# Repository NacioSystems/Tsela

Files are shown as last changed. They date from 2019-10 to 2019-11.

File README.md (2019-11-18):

# Tsela
## de NacioSystems:

Versión 1.3
Fecha: 31/10/2019

Este proyecto es un vehículo autónomo llamado **Tsela** (Tesela), que es capaz de conducir sin piloto por una pista de *siguelineas*. Realizado por NacioSystems (O Milladoiro):

Es un proyecto que tenía pensado desde hace un par de años, al ver las competiciones de siguelienas en la **Oshwdem Coruña**, y ver que todos los vehículos giran sobre dos o cuatro ruedas, pero forzando la velocidad de un lado respecto del otro, cuando en la práctica, salvo los vehículos con cadenas, todos los vehículos se mueven girando uno de los ejes, normalmente el delantero, haciendo coincidir la direccion de las ruedas delanteras con la secante de la curva.

Realmente al ver el resultado final, y las aprariencias del modelo, se me ocurrió llamarle Nisan Patrol, pero ese nombre ya estaba pillado. Me acordé también de Nicola Tesla, un pionero de los generadores eléctricos, pero el nombre tambien estaba pillado. Entonces recordé que las teselas, esos elementos geométricos que forman parte de la naturaleza, que fueron uno de los retos de la Oshwdem hace un par de años, podrían ser la clave. Así que me pareció muy apropiado el nombre de Tesela. Para abreviar, _**Tsela, Modelo 3, con Autopilot**_. :-)

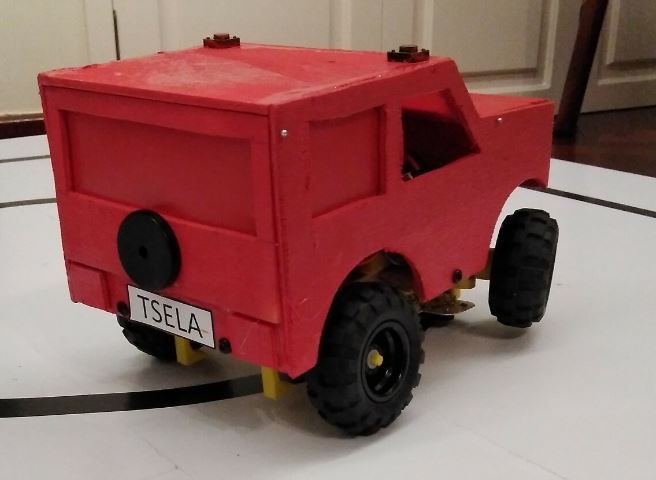
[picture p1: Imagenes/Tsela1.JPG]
Tesla Tsela M3 con Autopilot


- - -

### Introducción:

El chasis del vehículo está construido totalmente en madera, utilizando sobrante de madera de una caja de vino. Como motores utiliza dos micrometal que encontré perdidos y de los que desconozco su relación de reducción, aunque puedo decir que son muy potentes y poco veloces. Para controlar la velocidad de los motores utilizo un *driver* puente en H tipo **L298N**, que me permite regular la velocidad y el sentido de los dos motores. Por otra parte para leer la posición del vehículo respecto de la línea (negra) que debe seguir, utilizo una batería de cuatro sensores **CNY70**, puestos de modo transversal a la línea. Todo el conjunto está controlado por un **Arduino Nano** montado sobre una placa de expansión. La gracia del vehículo respecto de otros siguelíneas tradicionales, a parte de su bonito diseño totalmente artesano, es que gira gracias a un eje directriz delantero movido por un microservo **SG90**. Se alimenta todo el conjunto a través de dos baterías **LiPo 18650** puestas en serie, con 8V de tensión nominal.

El vehículo se enciende por un interruptor que da tensión al *driver* de los motores y a la placa Arduino. La marcha se inicia pulsando un botón que pone el vehículo en estado *Autopilot*, que se encuentra en el techo, iniciando el movimiento hacia adelante y leyendo lo sensores infrarrojos. En función de la señal que reciba de los sensores, en caso de no estar centrado sobre la línea, manda una señal al microservo de la dirección para corregir la posición y centrarse en la línea.

A través del puerto serie permite la **conexión remota por _Bluetooth_** y la gestión del vehículo, desactivando el *Autopilot* previamente. En caso de estar activado el _Autopilot_ no seguirá las instrucciones del piloto, salvo que no encuentre una línea a seguir, en ese caso, si encuentra una línea a seguir, tendrá prefrencia el seguimiento de la línea.

Si se toma el control por Bluetooth (9600,N,1), el Autopilot se puede activar o desactivar enviando el caracter 'P'. Es recomendable poner la aplicacion Bluetooth en modo repetitivo, con lo que se consigue girar progresivamente o acelerar mientras se pulsa botón correspondiente de la app. (ejemplo Bluetooth spp pro). Otras funciones implementadas para el contros serie son:
* 'A' Avanza más rápido, acelera
* 'R' Reduce la velocidad, decelera
* 'D' Mueve la dirección hacia la derecha, muy poco respecto de la posicióin actual
* 'I' Mueve la dirección hacia la izquierda, muy poco respecto de la posición actual
* 'P' Cada pulsación cambia entre modo _Autopilot_ o modo manual
* '0' Para los motores y pone la dirección recta
* 'C' Toca el claxon

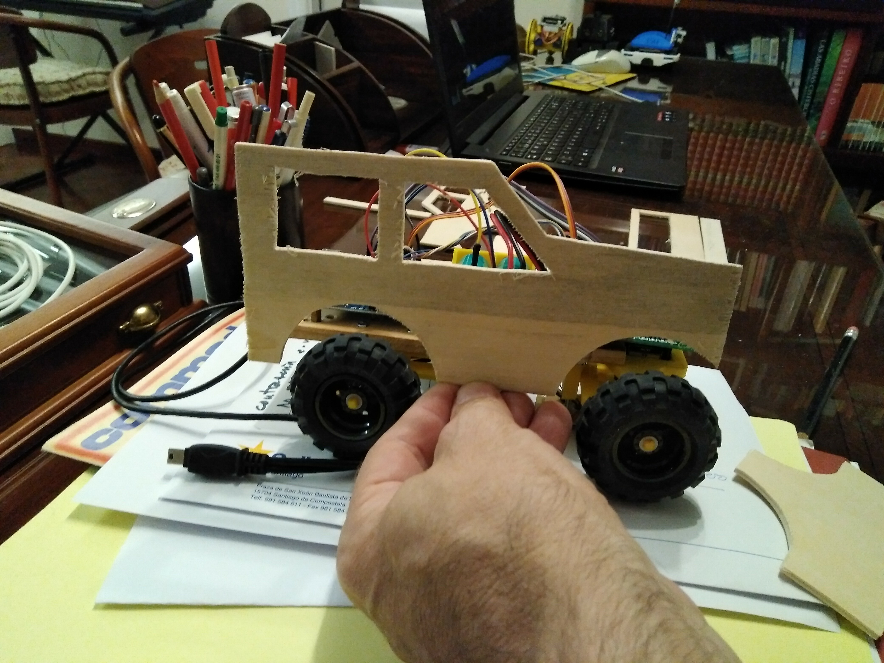
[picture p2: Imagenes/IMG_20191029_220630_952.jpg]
Imagen Tesla Tsela en construcción


Los sensores infrarrojos están montados sobre una placa improvisada, utilizando una tarjeta comercial tipo, numerados de izquierda a derecha del 1 al 4. Cuando el vehículo está centrado los sensores centrales 2 y 3 estarían sobre la línea negra, devolviendo muy poca señal al sensor, mientras que el resto de los sensores, 1 y 4 estarían sobre el blanco de la pista, devolviendo mucha señal al sensor. El sensor sobre la pista puede estar en 8 posiciones distintas:
* 1)- Sensor 1 en negro y resto en blanco. Vehículo muy desviado a la izquierda
* 2)- Sensor 1 y 2 en negro y resto en blanco. Vehículo desviado a la izquierda
* 3)- Sensor 2 en negro y resto en blanco. Vehículo ligeramente desplazado hacia la izquierda
* 4)- Sensores 2 y 3 en negro y 1 y 4 en blanco. Vehículo centrado, posición ideal
* 5)- Sensor 3 en negro y resto en blanco. Vehículo ligeramente desviado a la derecha
* 6)- Sensor 3 y 4 en negro y resto en blanco. Vehículo desviado a la derecha
* 7)- Sensor 4 en negro y resto en blanco. Vehículo muy desviado a la derecha.
* 8)- Todos los sensores sobre blanco, fuera de pista

Placa receptores infrarrojos Batería de sensores infrarrojos

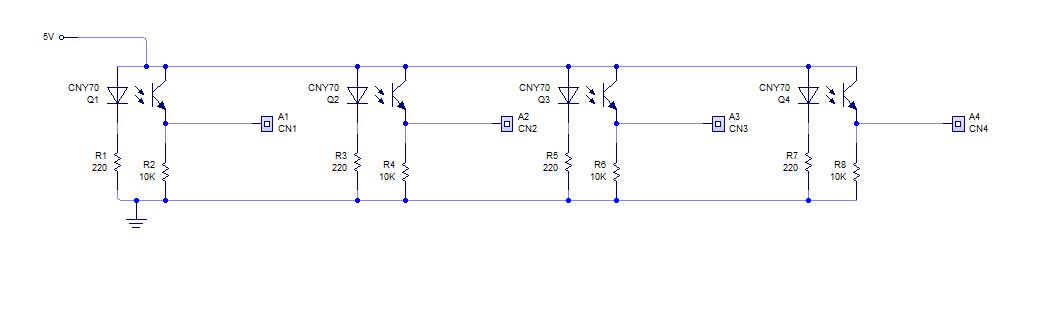
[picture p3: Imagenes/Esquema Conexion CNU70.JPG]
Esquema conexionado sensores infrarrojos Esquema de conexionado


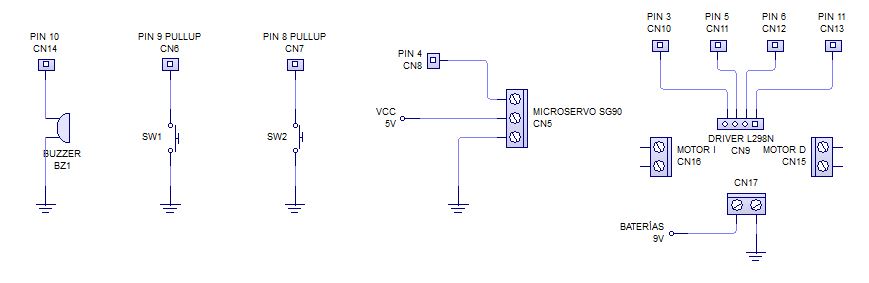
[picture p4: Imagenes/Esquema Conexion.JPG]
Esquema conexión pines Esquema conexionado pines


Conociendo la ubicación del vehículo sobre la pista, el sistema de control puede actuar sobre los motores y la dirección para corregir la posición, si es necesario, siendo los giros más cerrados cuanto más desviado está de la posición ideal, que sería cuando el vehículo está centrado.

Si el vehículo está centrado avanza recto a la máxima velocidad, pero cuando llega a una curva, detecta que es un giro por la posición de los sensores y decide reducir la velocidad y girar el eje delantero para corregir la posición.

Si la curva es muy cerrada y va muy rápido, detectará el cambio de dirección pero es posible que pierda la señal de la línea negra, lo que sería una situación fuera de pista, entonces mantendrá una velocidad más reducida y la dirección girada totalmente hasta que recupere la línea y pueda seguir el camino.

### Materiales y materiales reciclados:
El vehículo utiliza los siguientes materiales reciclados, que se pueden visualizar en las imágenes:
* Chasis y bastidor totalmente de madera, de una vieja caja de vino
* La placa que soporta los sensores es una tarjeta comercial tipo tarjeta de crédito.
* Los ejes de la dirección son metálicos de un viejo camión de bomberos de juguete
* Las ruedas son de un _quad_ Lego en desuso
* El altavoz _Buzzer_, también recuperado de un viejo juguete, que va en el portón trasero
* Parte del cableado está basado en líneas de pares telefónicos reutilizados y cable bililar de audio
* Las baterías LiPo 18650 son recuperadas de un viejo portátil que iba al desguace
* Parte de la tornillería es de una vieja impresora HP Laserjet que tambien se envió al desguace
* Los bornes y muelles del portabaterías son reutilizados de un control remoto de TV que no funcionaba
* Para las bisagras del portón trasero y del capó delantero utilizo alfileres del empaquetado de los que traen la camisas de vestir
* Los cristales tintados son trozos recortados de una separata de plástico, de las que se utilizan en carpetas de anillas perforadas.

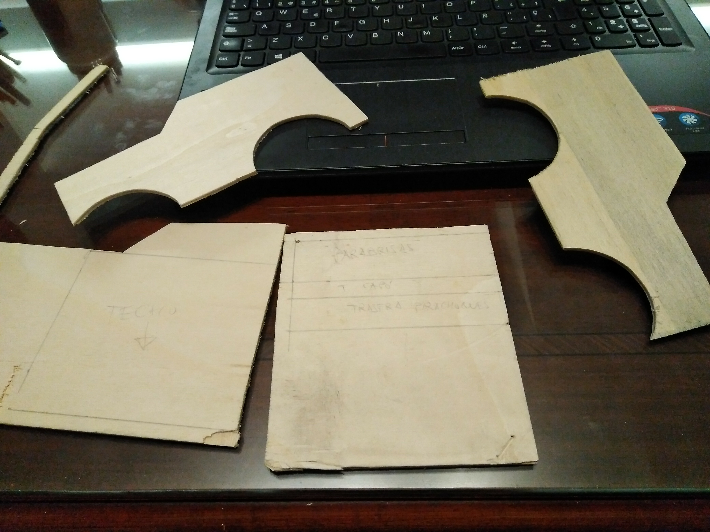
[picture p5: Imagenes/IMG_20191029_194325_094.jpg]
Foto Maderas cortadas Preparando la carrocería


Otros materiales:

También se han utilizado piezas impresas en 3D, para hacer la dirección, puesto que no servía ninguna dirección adecuada para este vehículo. La dirección es diseñada totalmente por mi, para integrar el Servo SG90, los ejes de dirección metálicos disponibles y las ruedas de Lego. Otras piezas impresas son la caja soporte de las baterías, también diseñada por mi y las piezas soporte de los motores al chasis. Para las piezas impresas he utilizado nueva tornillería de métrica M3.

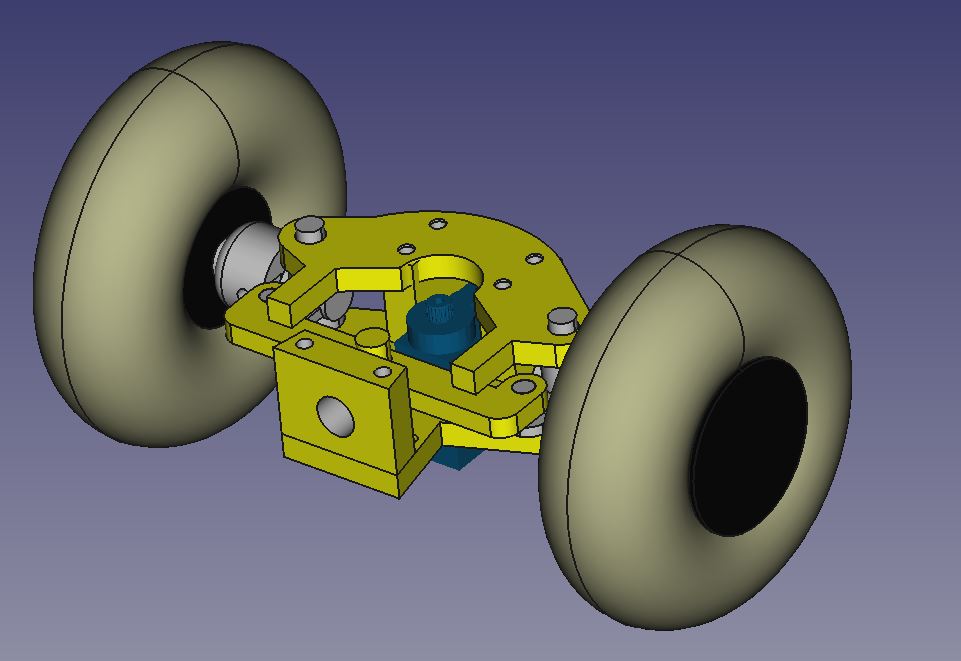
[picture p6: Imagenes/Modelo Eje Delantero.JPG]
Diseño sistema dirección Eje delantero


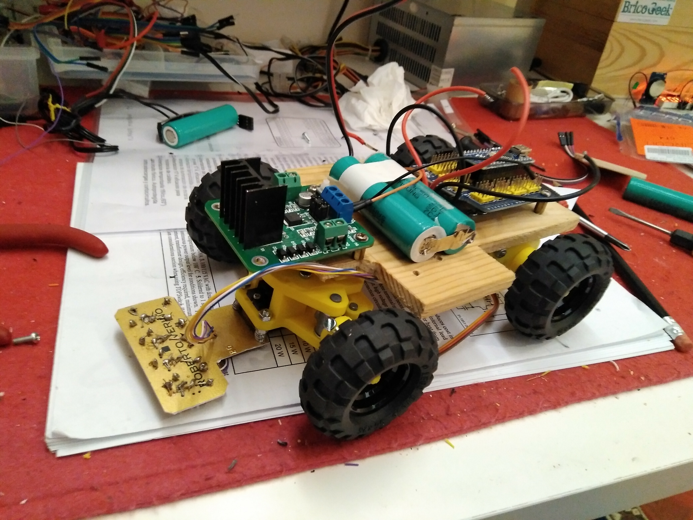
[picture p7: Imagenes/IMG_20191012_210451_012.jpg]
Foto Tsela sin carcasa Prototipo 2


Materiales electrónicos:

* [Arduino Nano][2]
* [Extension Board Arduino Nano][3]
* [Puente H L298N][4]
* [2 x Micrometal Gear. Micromotores 6V][5]
* [Microservo SG90][6]
* [4 Sensores infrarrojos CNY70][7]
* [2 LiPo 18650 de 3,7V][8]
* 2 pulsadores y un micorinterruptor
* Buzzer
* Algunas resistencias para la polarización de los CNY70 y la medición del estado de las baterías (sin implementar por A0)
* Otro pequeño material como bornas para la conexion de la batería y PCB prototipo para el montaje de interruptor y botones.

### Pista:
La pista del circuito a recorrer está montada en un tablero de 2x2m2, de color blanco, en el que se traza una línea negra de 1,9cm de ancho, que será la que marque el circuito a recorrer.

El recorrido del circuito es cerrado, los puntos de salida y llegada son el mismo. Tendrá una longitud aproximada de 4 metros e incluye rectas y curvas de diferentes radios. La curva de menor radio no será inferior a los 125 mm, y la distancia mínima entre dos partes próximas del recorrido no será inferior a los 250 mm. Las medidas y recorrido del circuito no se darán a conocer hasta el comienzo de la prueba.

Los vehículos (robots) deberán completar un recorrido completo en el menor tiempo posible.

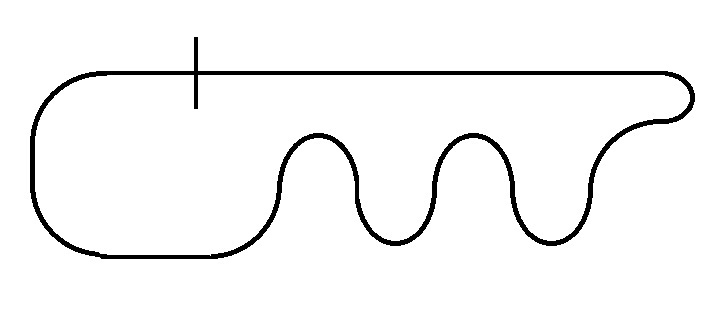
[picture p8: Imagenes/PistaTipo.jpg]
Foto Pista Modelo Pista


### Condiciones iniciales:
En el inicio de la competición el vehículo se sitúa centrado sobre la línea del circuito, en la dirección a recorrer. El interruptor de encendido debe estar en **ON** y en el momento de salida habrá que iniciar el camino pulsando el botón de *Autopilot*. Deberá realizar el recorrido en el menor tiempo posible sin salirse del circuito y recorriéndolo completamente. Una vez terminado el recorrido se puede desactivar el modo _Autopilot_ pulsando nuevamente en el botón correspondiente, o a través de Bluetooth de ser el caso.

### Desplazamientos y giros:
Una vez puesto en marcha el vehículo inicia su movimiento a la máxima velocidad, manteniendo la dirección si está centrado. En el momento que detecta que no está centrado, inicia un giro del eje delantero, a través del Microservo SG90 para corregir su posición. Una vez se encuentra centrado de nuevo, el robot devuelve la dirección del eje delantero para continuar en línea recta.

### Programa:
El programa está realizado con el IDE Arduino, para su programación directa a través de cable USB. En la carpeta software se puede ver el programa comentado. El programa cuenta con una pestaña de _"configuracion.h"_, en donde está el _pineado_ para las conexiones con el Arduino (sensores, microservo, botones, buzzer) para ajustar los valores por defecto, que dependerán de los motores y sensores utilizados en cada caso, si son diferentes a los de esta construcción. El programa está estructurado y comentado con lo que resulta fácil su comprensión, mantenimiento y modificación.

### Construcción:
El resultado final es la progresión de varias experiencias sobre el modelo inicial trabajando únicamente sobre un bastidor de madera, al que fui añadiendo modificaciones según iban apareciendo las complicaciones o para simplificar problemas. El primer vehículo llevaba motores chinos sobre una plataforma de madera más larga, en la que fui acoplando ejes delanteros de giro de varios coches de juguete, accionados por un microservo y palancas de reenvío. 

Ante el fracaso continuo con el sistema de dirección, especialmente por las holguras y el corto ángulo de giro,  me propuse aprovechar parte de uno de los ejes de un juguete que había usado para construir un nuevo sistema delantero de dirección, utilizando _FreeCad_. El resultado espectacular. Un único inconveniente, el vehículo resulta muy largo y limita el ángulo de giro. Las primeras pruebas las hago sin sensores, moviendo el vehículo a través de un control por Bluetooth y comprobando su comportamiento con control manual. Primer objetivo reducir la longitud del bastidor para mejorar el ángulo de giro, para llegar a los 12,5cm de radio de giro de la Oshwdem.

A esta segunda versión ya le incorporo todos los elementos electrónicos, incluyendo el sensor de líneas. Este sensor iba situado muy avanzado delante de eje de dirección, para anticiparse a las curvas. Después de muchos ajustes, placa controladora, baterías, dirección, driver de motores, vemos que queda espacio para reducir más la longitud del bastidor. Aparece un nuevo problema, en curvas cerradas, el sistema de dirección gira bien, pero la velocidad es muy alta y los motores no tienen la calidad suficiente para mantener el empuje con valores pequeños de **_PWM_**. En curvas cerradas el vehículo se queda por falta de empuje o sale disparado fuera de la pista por mucha potencia en los motores. Decisión, cambiar motores.

En una nueva versión ya incorporo un soporte para las baterías impreso en 3D y diseñado en _FreeCad_ **(Gracias por tus microtutoriales Obijúan)**

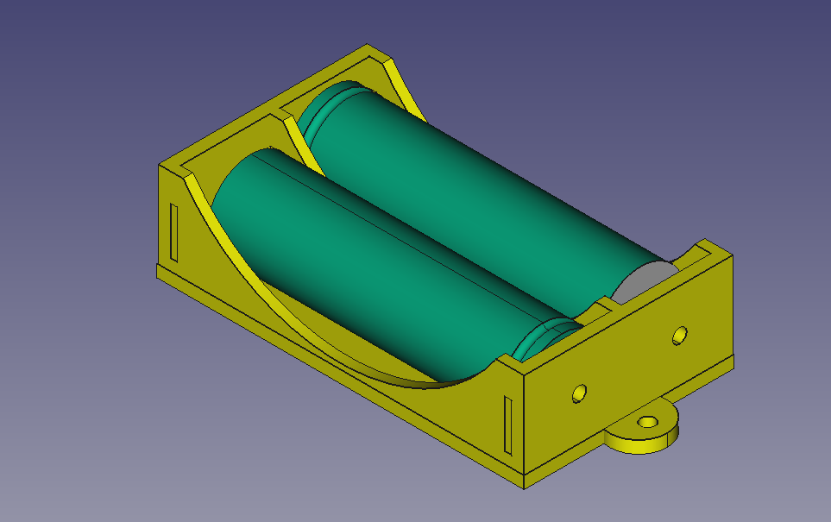
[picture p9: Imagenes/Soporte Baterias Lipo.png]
Foto portabaterías LiPo Portabaerías


El cambio de motores supone también la necesidad de un sistema de acople a la carrocería. Se resuelve con un diseño en _Freecad_ de nuevas piezas que abrazan lon motores al bastidor de madera y permiten la incorporación de amortiguadores, listas para imprimir en 3D. En esta versión también se comprueba la viabilidad de acercar el sensor para ponerlo debajo del tren delantero. El resultado es prometedor, el vehículo recorre perfectamente circuitos muy complejos sin salirse de la pista, aunque todavía pegando bandazos en la dirección. 

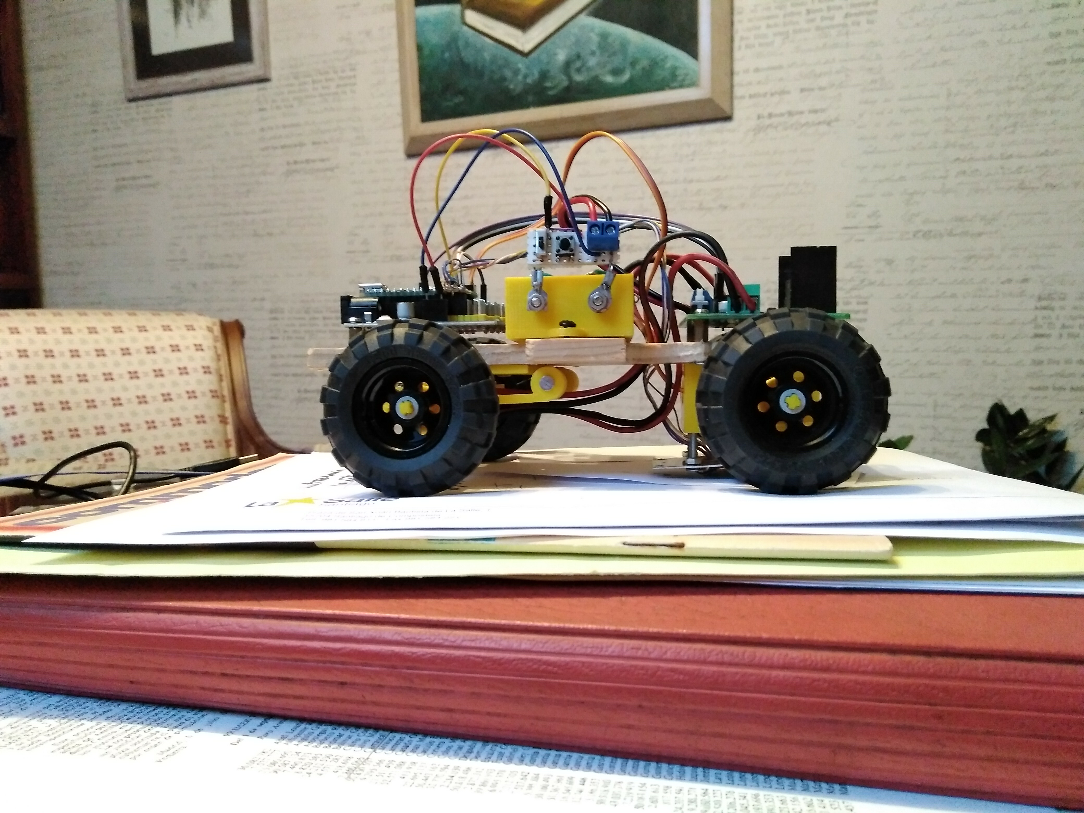
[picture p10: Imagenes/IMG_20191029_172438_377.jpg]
Nuevo Tesela Nuevo Tsela


Para el ajuste de los motores incorporo una bola metálica delantera que levanta el tren de dirección. De esta manera Tseo puede funcionar siguiendo las lineas por el método tradicional, cambiando la velocidad de los motores derecho e izquierdo para centrarlo en la línea. Una vez ajustada esta velocidad se puede suprimir la bola metálica y dejando los giros en manos de la servo-dirección, ya suavizada, actuando los motores a modo de ASR, control de la tracción para evitar el deslizamiento. Los bandazos de la dirección se suavizan haciendo una media entre la posición del servo en la dirección anterior y la nueva dirección:

```c
// SalidaPinDir es el valor que ponemos al servo
//SPD_Anterior es el anterior valor que tenía el servo
// Calculamos la media con la anterior
  SalidaPinDir=(SalidaPinDir+SPD_Anterior)/2;
  // Ahora la anterior pasa a ser la actual
  SPD_Anterior=SalidaPinDir;
```

A partir de aquí empiezo a construir la carrocería, dibujando directamente las medidas que tomo en el chasis sobre la madera y cortando con una sierra de calar. Unimos las piezas con cola blanca para madera, lo lijo y lo pinto de color rojo con _spray_. El portón trasero es abatible, lo que permite acceder al puerto USB para la programación del Arduino Nano. Tambien se abre el capó delantero, dando acceso al *driver* de los motores, y el botón de desconexión del *driver*, muy práctico para hacer pruebas sobre la línea sin moverse.

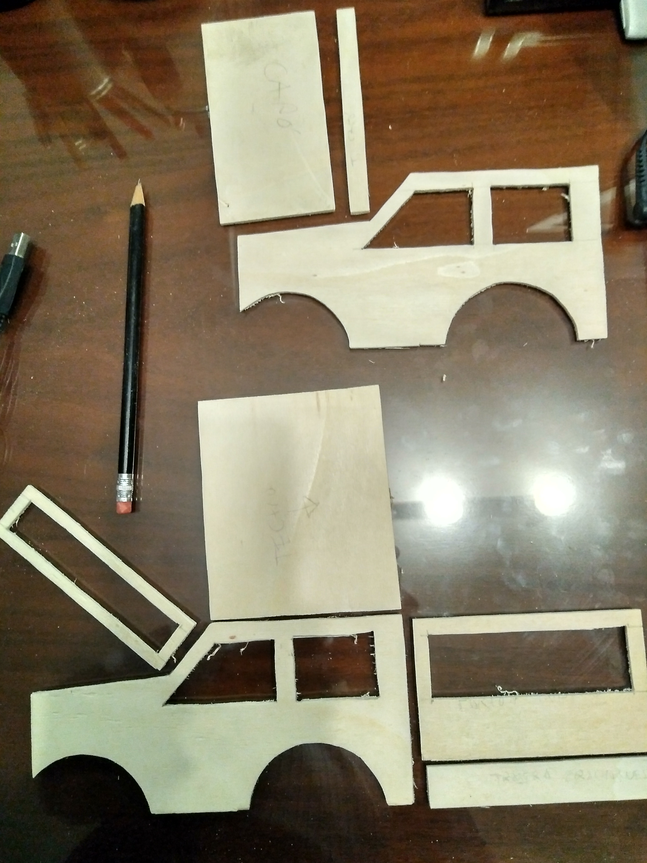
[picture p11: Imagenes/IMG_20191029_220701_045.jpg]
Foto chasis en construcción Piezas madera cortada


En esta versión se incorporan dos botones en el techo del vehículo, uno, el de la izquierda si miramos en el sentido de avance, es el que activa y desactiva el _Autopilot_, lo que permite el arranque y parada en competición. El otro, el de la derecha y que en la actualidad activa el _claxón_, está pensado para futuras ampliaciones, encendido de luces, cambio de estado, etc.

Se incluyen en los archivos _FreeCad_ el diseño de la carrocería en 3D, por si alguien quiere ver las dimensiones de las piezas o imprimirla en material plástico en vez de recortar madera.

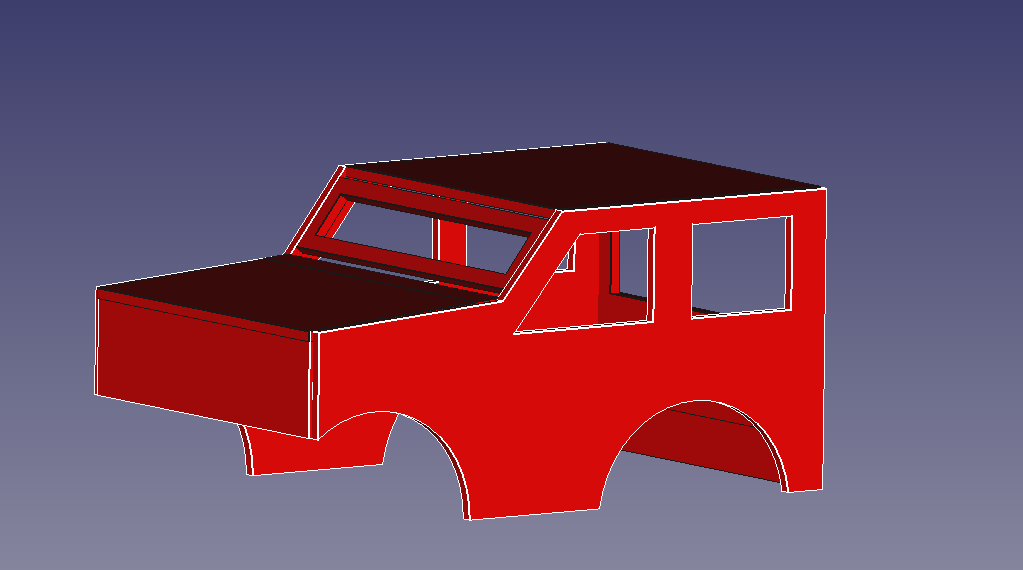
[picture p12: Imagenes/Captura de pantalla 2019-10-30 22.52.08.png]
Diseño carrocería Carrocería


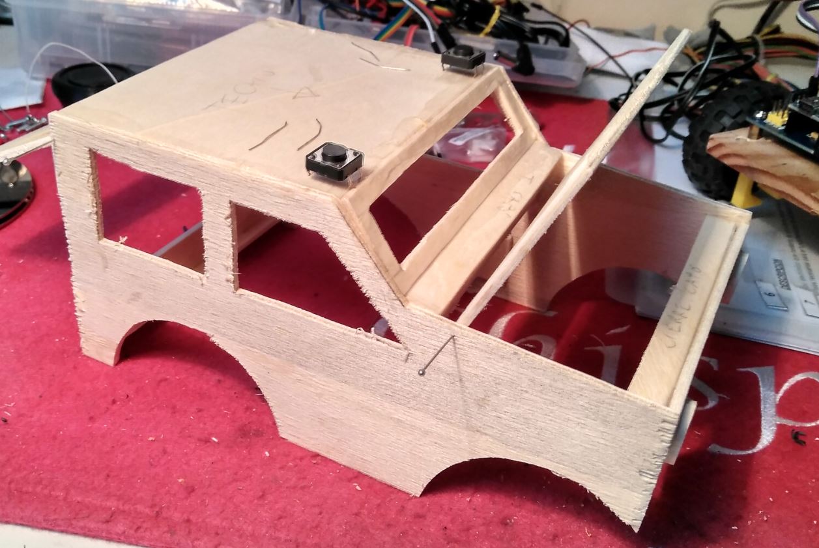
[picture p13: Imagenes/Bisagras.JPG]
Montaje carrocería


### Piezas impresas:
* [Caja baterías][10]
* [Dirección eje delantero][11]
* [Soporte motores traseros][12]

[10]: https://github.com/NacioSystems/Tsela/blob/master/Imagenes/Soporte%20Baterias%20Lipo.png
[11]: https://github.com/NacioSystems/Tsela/blob/master/Imagenes/Modelo%20Eje%20Delantero.JPG
[12]: https://github.com/NacioSystems/Tsela/blob/master/Imagenes/Soporte%20Micromotores.png

### Pendiente:
En este momento tengo pendiente de incorporar otras funcionalidades:
* Medir el estado de las baterías LiPo 18650, para informar del cambio de baterías cuando la tensión baja de 3.7V
* Incorporar luces *LED* de posición delanteras (blancas) y traseras (rojas), así como de dirección (intermitencias amarillas)
* Controlar el encendido y apagado de los sensores IR mediante un transistor controlado por pin 10
* Incorporar un cargador de dos celdas para LiPo, para poder cargar las baterías por USB o fuente externa sin tener que sacar la carrocería.

### Referencias:
* *[Página Web **OSHWDEM**][9]*

* *[Tutorial para construir un robot siguelineas con material reciclado][1]*

* *[Arduino Nano][2]*

* *[Extension Shield Arduino Nano en Amazon][3]*

* *[Driver motores, puente H L298N en Amazon][4]*

* *[Micrometal Gear Motor en BricoGeek][5]*

* *[Microservo SG90 en PC Componentes][6]*

* *[Sensor infrarrojos CNY70 en Amazon][7]*

* *[Baterías Lipo 18650 en Alibaba][8]*

### Autor:

**Ignacio Otero**

### Agradecimientos:

Muchas gracias **Bea** por tu colaboración en la revisión y corrección de esta página.

### Licencia:

Todos estos productos están liberados mediante Creative Commons Attribution-ShareAlike 4.0 International License.

[1]: https://todohacker.com/tutoriales/tutorial-robot-siguelineas
[2]: https://store.arduino.cc/arduino-nano
[3]: https://www.amazon.es/Ociodual-ATmega328P-Extension-Compatible-Arduino/dp/B07FN2Z5K7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
[4]: https://www.amazon.es/HarmonyHappy-L298N-Motor-Drive-Modulo/dp/B07V7DHC2F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
[5]: https://tienda.bricogeek.com/motores/113-motor-micro-metal-lp-con-reductora-10-1.html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
[6]: https://www.pccomponentes.com/servo-sg90-micro-servo-9g-compatible-con-arduino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
[7]: https://www.amazon.es/s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
[8]: https://www.alibaba.com/product-detail/Best-Quality-Of-ISR-Lithium-Rechargeable_60779827115.html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
[9]: https://oshwdem.org/

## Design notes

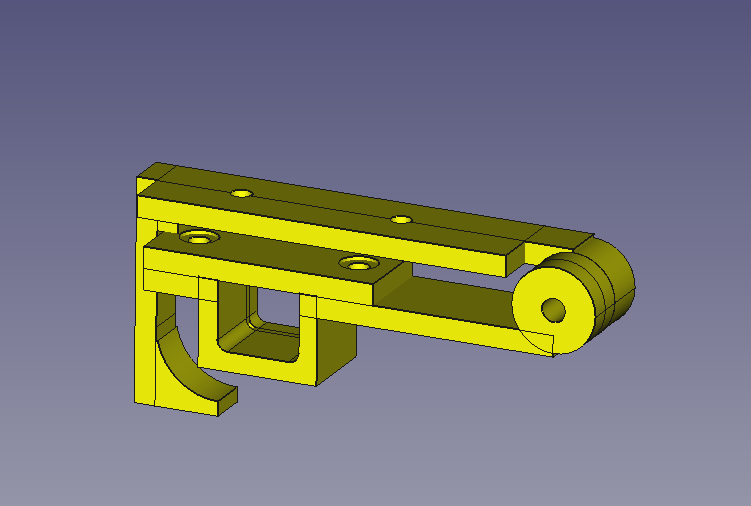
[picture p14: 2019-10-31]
Imagenes/Soporte Micromotores.png

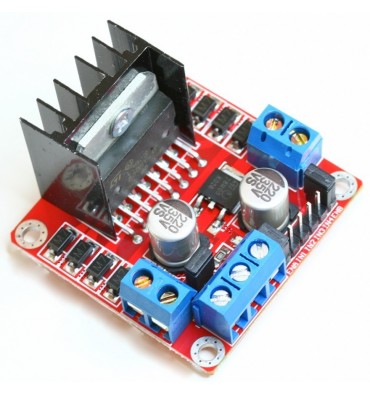
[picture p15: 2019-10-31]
Imagenes/l298n.jpg

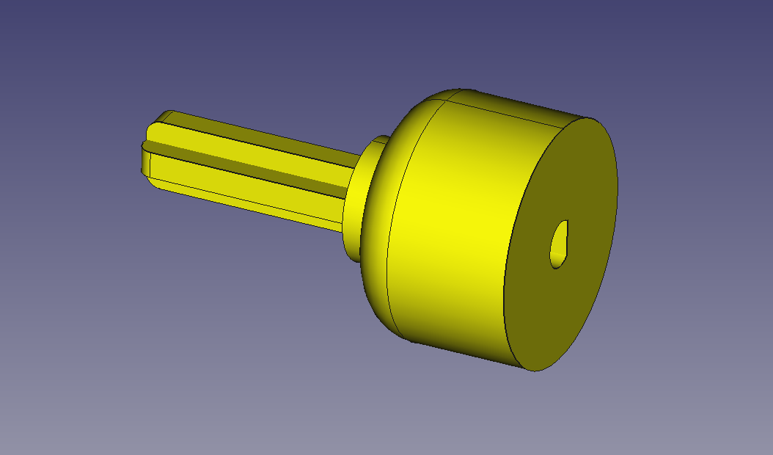
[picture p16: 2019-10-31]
Imagenes/Eje conexion Lego Micromotor.png

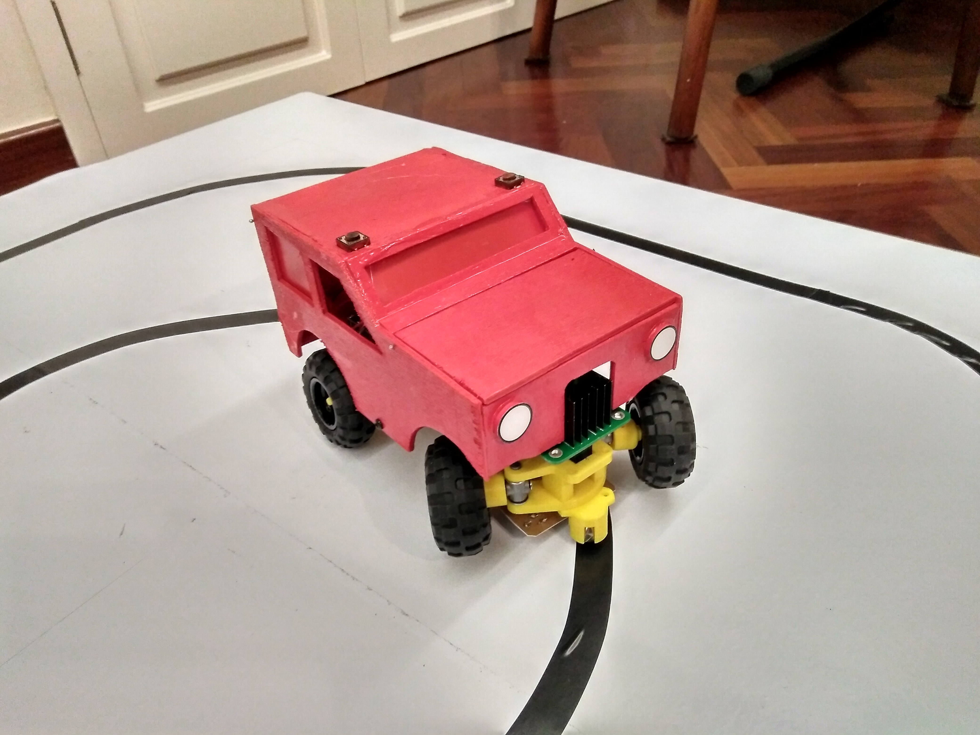
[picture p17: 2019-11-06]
Imagenes/Tsela2.jpg

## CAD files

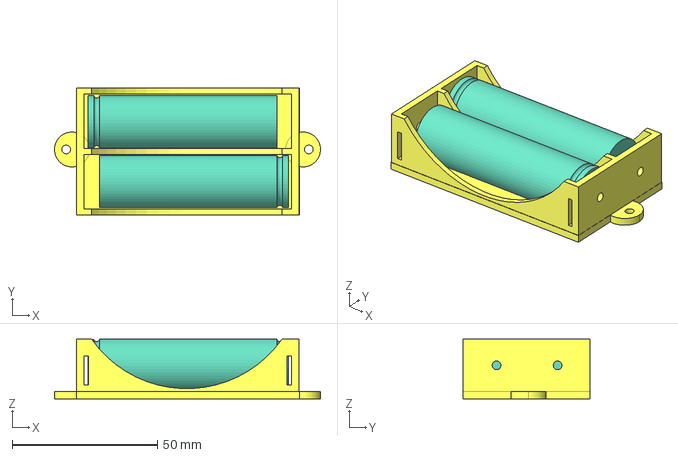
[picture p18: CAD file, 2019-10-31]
FreeCad/CajaBateriaLipo.FCStd
91.5 x 43.8 x 20.5 mm
Porta Lipo 2S
Baterias

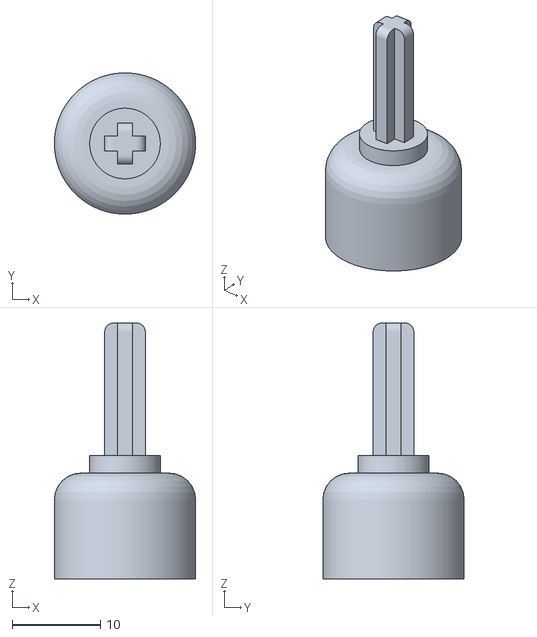
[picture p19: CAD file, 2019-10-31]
Partes Impresas/Eje rueda motor chino.stl
16.0 x 16.0 x 29.0

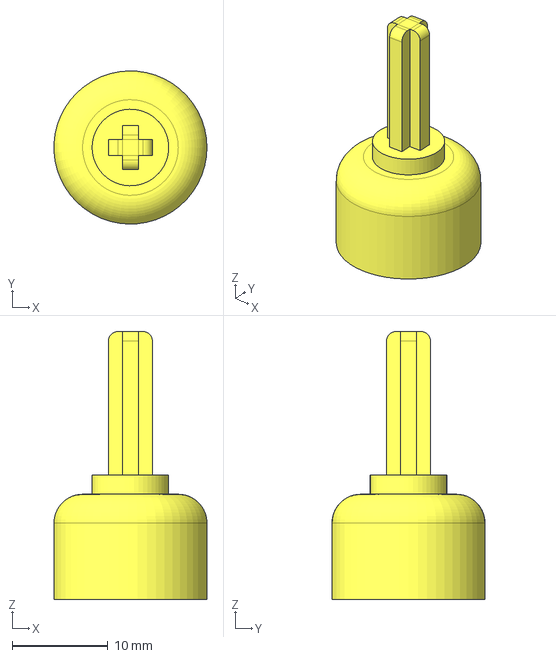
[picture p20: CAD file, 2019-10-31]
FreeCad/EjeTransmisionMinimotor.FCStd
16.0 x 16.0 x 28.0 mm

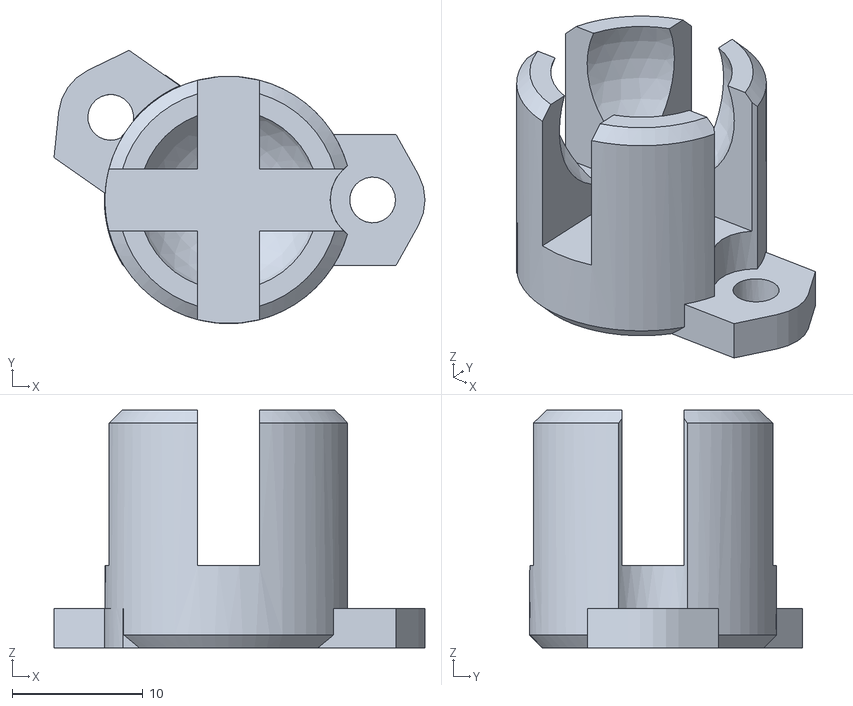
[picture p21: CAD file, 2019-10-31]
Partes Impresas/Portabola.stl
28.3 x 20.9 x 18.2

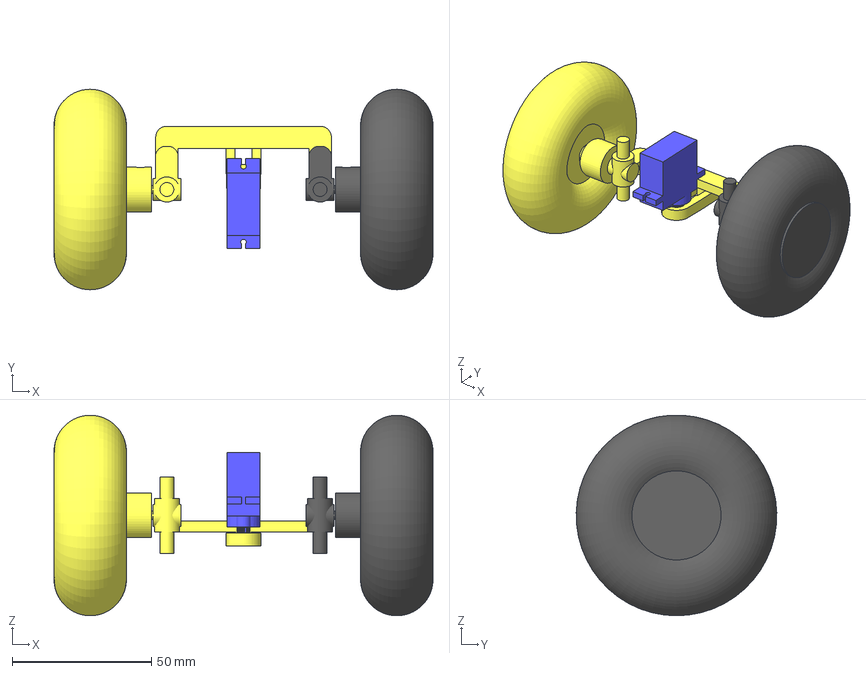
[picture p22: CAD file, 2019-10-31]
FreeCad/Direccion V2.FCStd
136.0 x 72.0 x 71.9 mm
Horquilla
Servo-SG90

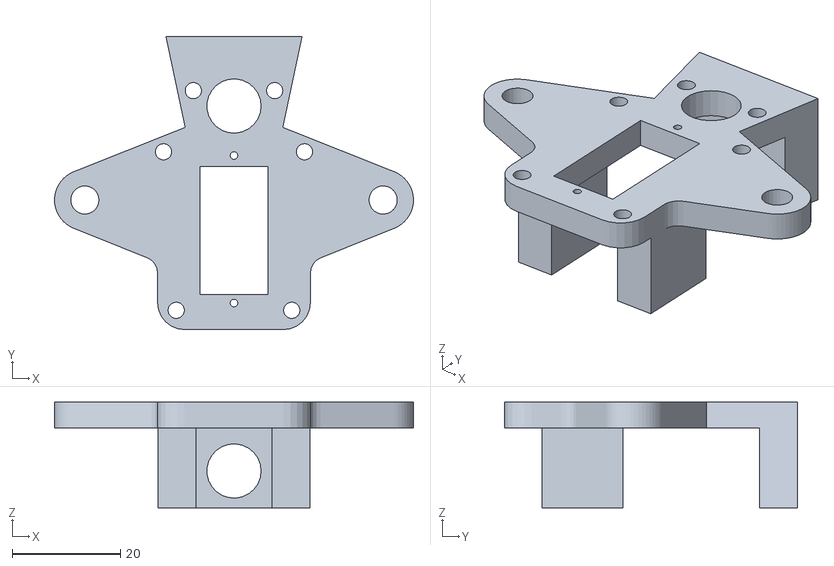
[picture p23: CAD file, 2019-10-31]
Partes Impresas/Carter inferior2.stl
66.2 x 54.1 x 19.5

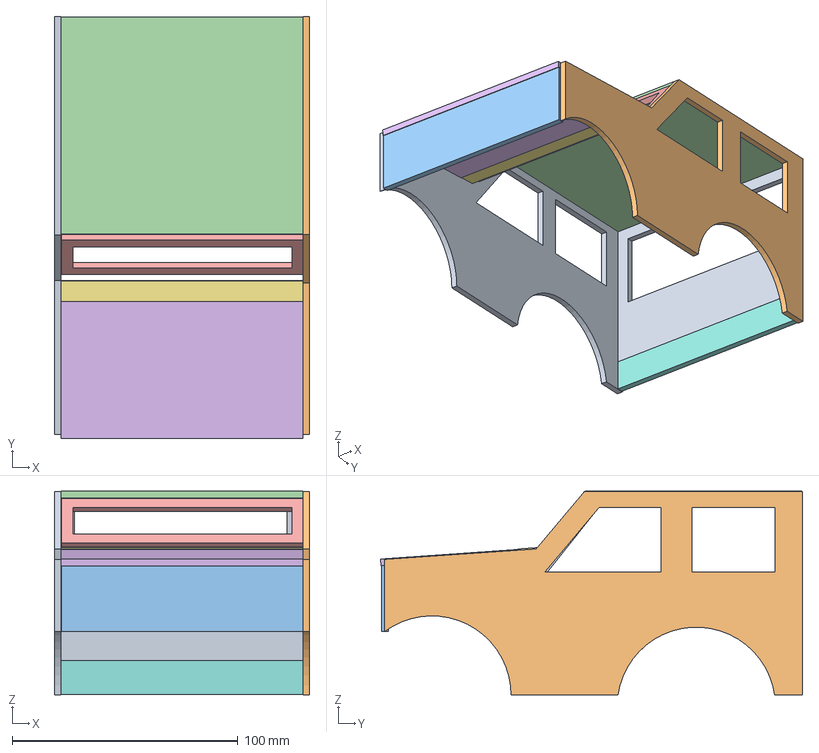
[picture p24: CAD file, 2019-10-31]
FreeCad/Esquema carroceria.FCStd
113.0 x 186.8 x 90.3 mm
Cubo
Cubo001
Cubo002
Cubo003

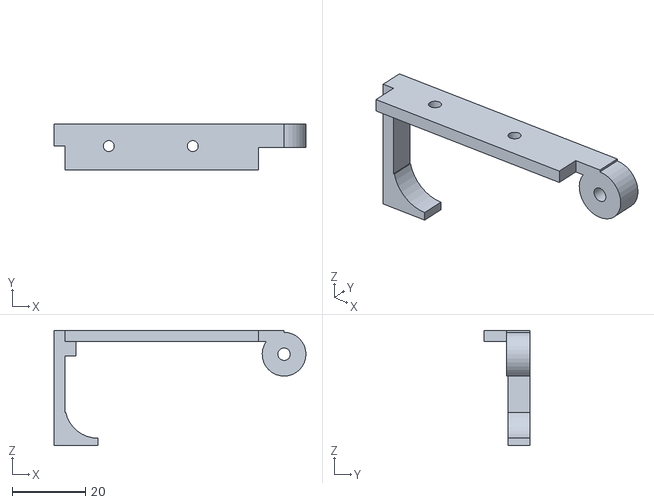
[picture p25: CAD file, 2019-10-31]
Partes Impresas/Base Motor Superior.stl
69.0 x 12.5 x 31.5

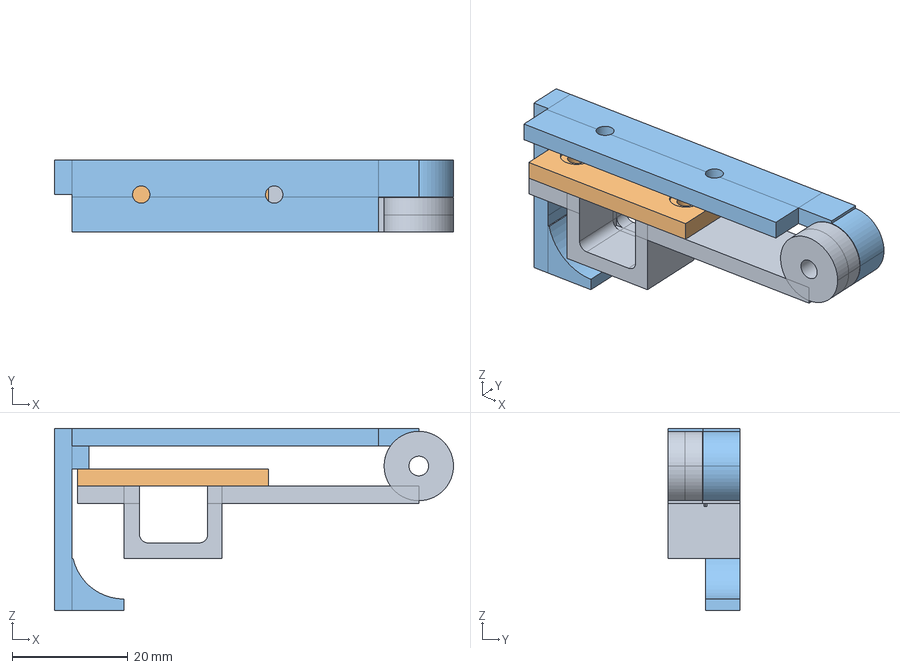
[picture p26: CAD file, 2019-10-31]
FreeCad/Soporte Motor 1.FCStd
69.0 x 12.5 x 31.5 mm
Base inferior tuercas
Tapa con tornilleria
Base superior tuercas

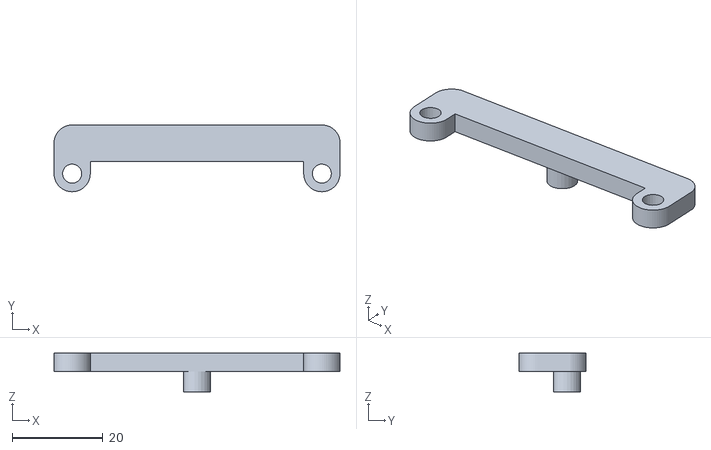
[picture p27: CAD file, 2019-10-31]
Partes Impresas/barra direccion.stl
63.0 x 14.7 x 8.50

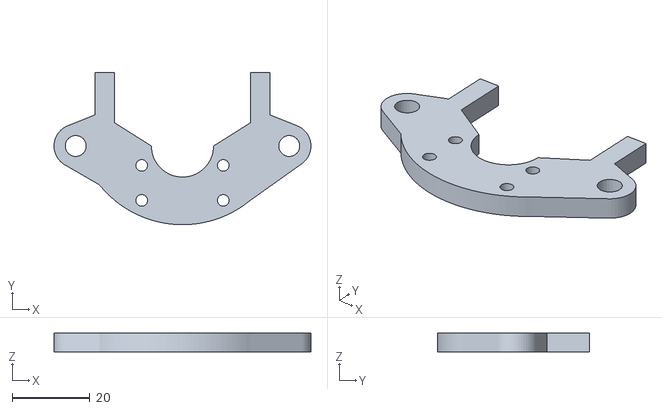
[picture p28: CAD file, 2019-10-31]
Partes Impresas/Carter superior.stl
66.2 x 39.3 x 4.80

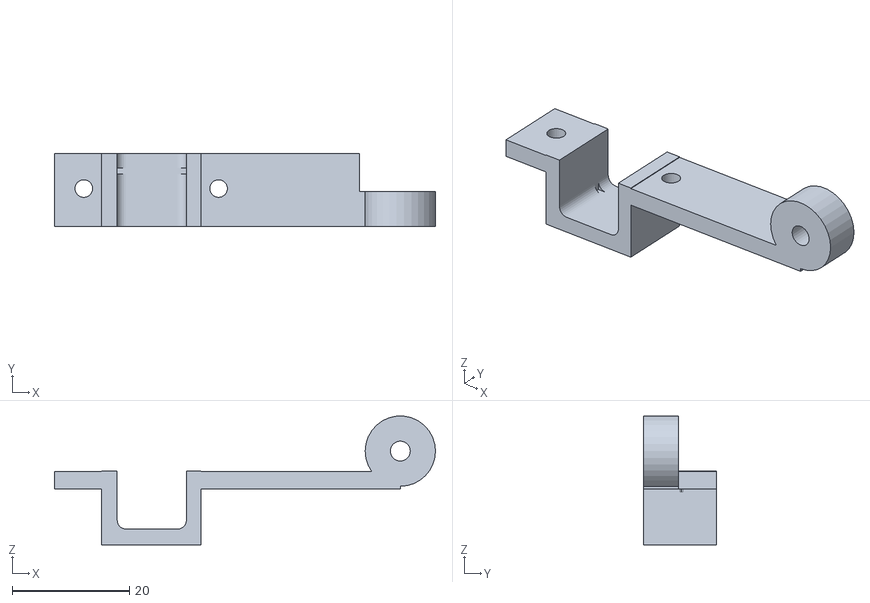
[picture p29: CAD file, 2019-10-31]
Partes Impresas/Base Motor Inferior.stl
65.0 x 12.5 x 22.0

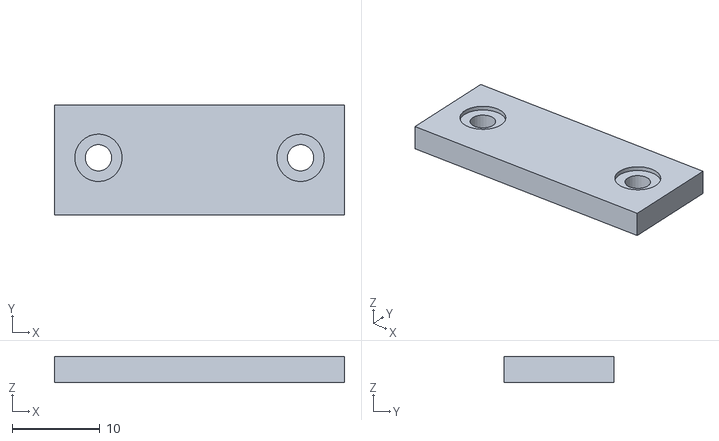
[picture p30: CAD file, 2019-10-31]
Partes Impresas/Base Motor Tapa.stl
33.0 x 12.5 x 3.00

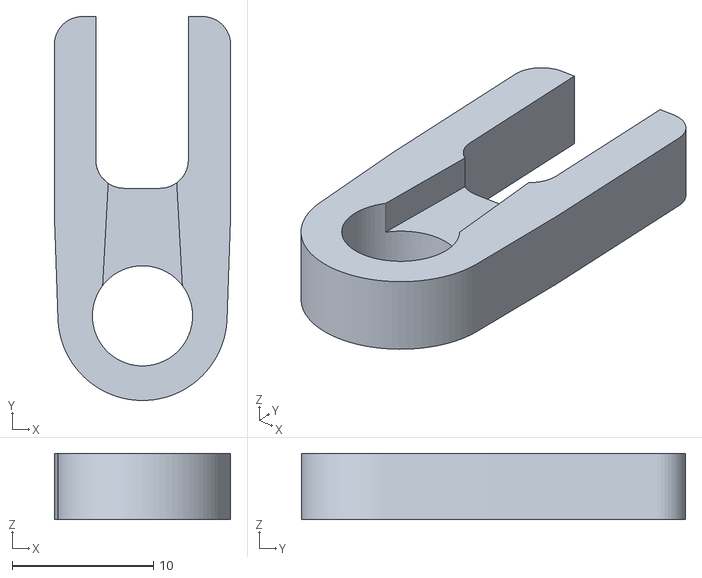
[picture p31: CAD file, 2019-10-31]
Partes Impresas/Horquilla.stl
12.5 x 27.2 x 4.70

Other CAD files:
Partes Impresas/Carter inferior.stl
Partes Impresas/Carter inferior3.stl
Partes Impresas/EjeTrasero.stl
Partes Impresas/Eje rueda Delantera.stl
Partes Impresas/Soporte Lipo.stl

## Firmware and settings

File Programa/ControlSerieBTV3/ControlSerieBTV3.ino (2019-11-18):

// *******************************************************************************************************
// *******************************************************************************************************
// ********      PROGRAMA SIGUELINEAS DE IGNACIO OTERO CONCURSO OSHWDEM 2019 CORUÑA              *********
// *******************************************************************************************************
// *******************************************************************************************************
// ************       NOMBRE PROPUESTO DEL BICHO TESELA (¡---- --------!)                     *************
// *******************************************************************************************************
// *******************************************************************************************************
// Versión 9.3 Primera versión que funciona con bolita y sin bolita! 26/10/2019

// Parámetros configurables en "Configuracion.h"
/*
  Sistema de guiado a través de Bluetooth, para ajuste de siguelineas
  
  Lee los comandos que llegan por BT y ajusta la velocidad y dirección

  El circuito:
  -Control de motores conectados pines PWM 3,5,6,11
  -Control de servo conectado a pin 4
  -Entradas analógicas conectadas a pines A1, A2, A3, A4
 
  created 4 octubre 2019
  modified 24 octubre 2019
  Por Ignacio Otero

  
*/

#include "Configuracion.h"
#include <Servo.h>
Servo myservo;  // create servo object to control a servo


// Variables generales
boolean Autopilot = false;    // Indica el estado del vehículo, en movimiento o parado
int ValorPinDir = 0;      // Valor de lectura del potenciometro dirección
int SalidaPinDir = central;  // Valor de salida servo (-180,180) limitado en margen
                             // Los valores están comprendidos entre central-margen y central+margen (50, 120)
                             // A parte del servo se van a utilizar para cambiar la velodidad de los motores
// Velocidades motores
int Vel_Motor_D=0;
int Vel_Motor_I=0;
                             
int ValorPinVel = 0;      // Valor de lectura del potenciómetro velocidad
int SalidaPinVel = 0;     // Valor de salida de la velocidad (-255, 255). Negativo es inversa
                          // En siguelineas no vamos a trabajar con valores negativos para la dirección
                          // Probamos con el doble del valor de SalidaPinDir, de tal manera que:
                          //              - si es menor de 85, frenamos motor izquierdo Freno=2*(85-SalidaPinDir)
                          //              - si es mayor de 85, frenamos motor derecho   Freno=2*(SalidaPinDir-85)
                          //              - Evidentemente si no hay freno ponemos       Freno=0
int pos = 0;              // Almacena el valor del servo  
int Freno=0;              // Valor de freno en cada momento

// Variables de sensores analógicos
int SensorD2=0;  // Sensor más a la derecha
int SensorD1=0;  // Sensor central derecha
int SensorI1=0;  // Sensor central izquierda
int SensorI2=0;  // Sensor central más a la izquierda
int Posicion=0;  // Estado de la posición de -3 a +3, o 999 fuera linea


void setup() {
  Serial.begin(9600);
 
  Serial.println(F("\n\n-------------------------------------------"));
  Serial.println(F("Configuración Zumo, versión 9.3, 25/10/2019"));
  Serial.println(F("             Ignacio Otero"));
  Serial.println(F("-------------------------------------------\n\n"));

  // Configuramos la entrada de Boton como pullup
  pinMode(BOTON, INPUT_PULLUP);

  // Colocamos servo en PinServo
  myservo.attach(PinServo);  // 
  
  // Dirección del servo al centro 
  myservo.write(SalidaPinDir);

  // Paramos motores
  Serial.println("Motores parados:");
  PonemosMotores(0,0); 
 
}

void loop() {
 // Leemos BT
 LeemosBT();

 // Leemos Botón
 LeemosBoton();

 // Leemos Sensores IR
 LeemosIR();
 
 // Calculamos la poiscion del sensor IR en la línea negra
 // Inicialmente esta función nos da el valor de SalidaPinDir y Velocidad
 // central-margen< SalidaPinDir < central+margen
 // -255 < Velocidad < 255 
 CalculamosPos();  

 // Colocamos la direcciòn de las ruedas por el servo
  myservo.write(SalidaPinDir);
      
  // Calculamos el freno en función del desvío del sensor a la línea negra
  // El freno será 0 cuando SalidaPinDir = central
  // El freno será la velocidad cuando SalidaPinDir=central+/-margen
  // -SalidaPinVel < Freno < SalidaPinVel
  Freno= SalidaPinVel*(central-SalidaPinDir)/margen;   // Aseguramos freno en el margen establecido
  Serial.print("\t Freno=");
  Serial.print("\t");
  Serial.println(Freno);  
    
   // Colocamos velocidad
   // SI EL FRENO ES POSITIVO MOVIMIENTO A LA IZQUIERDA
   if(Freno>=0){ // Fenamos motor I
         Vel_Motor_D=SalidaPinVel;
         Vel_Motor_I=SalidaPinVel-Freno;
         }
  
   // SI EL FRENO ES NEGATIVO MOVIMIENTO A LA DERECHA
   else {
         Vel_Motor_D=SalidaPinVel+Freno;
         Vel_Motor_I=SalidaPinVel;
         }
  // Solo tocamos la velocidad de los motores si estamos en Autopilot
  // En caso contrario es a través de BT como se controla la velocidad
   if(Autopilot) PonemosMotores(Vel_Motor_I,Vel_Motor_D);      
  
  // 
  delay(20);
}

//***********************************************
//****       FUNCIÓN LEEMOS BLUETOOTH        ****
//***********************************************
void LeemosBT() {
   char opcion = Serial.read();
  if (opcion == '0')  {
    SalidaPinDir= central;    
    SalidaPinVel=0;
  }
  else if (opcion == '1')  {
    SalidaPinDir= central;    
  }
  else if (opcion =='D') {
    SalidaPinDir=SalidaPinDir+5;
    if(SalidaPinDir<central-margen) SalidaPinDir=central-margen;
  }
  else if (opcion =='I') {
    SalidaPinDir=SalidaPinDir-5;
    if(SalidaPinDir>central+margen) SalidaPinDir=central+margen;
  }
   else if (opcion =='A') {
    SalidaPinVel=SalidaPinVel+10;
    if(SalidaPinVel>255) SalidaPinVel=255;
  }
   else if (opcion =='R') {
    SalidaPinVel=SalidaPinVel-10;
    if(SalidaPinVel<-255) SalidaPinVel=-255;
  }
  else if (opcion =='P') {
    Autopilot=!Autopilot;
  }

} // Fin función leemos BT


//***********************************************
//****   FUNCIÓN LEEMOS BOTÓN INICIO PARADA  ****
//***********************************************
void LeemosBoton() {
   if(!digitalRead(BOTON)) {
        Autopilot=!Autopilot;  // Cada vez que se pulsa cambia de estado
        if(Autopilot) Serial.println("\nAutopilot ON");
        else {
           Serial.println("\Autopilot OFF");
           // Paramos motores
           Serial.println("Motores parados:");
           PonemosMotores(0,0); 
        }
        delay(100);
   }
}


//***********************************************
//****  FUNCIÓN LEEMOS SENSORES INFRARROJOS  ****
//***********************************************
void LeemosIR() {

 // Leemos las entradas, menos de 100 está en la línea:
      SensorD2=analogRead(SIRD2);
      SensorD1=analogRead(SIRD1);
      SensorI1=analogRead(SIRI1);
      SensorI2=analogRead(SIRI2);
  

   // Ponemos el valor
  //Serial.println("A4 \tA3 \tA2 \tA1 \t\tPos \tDir \tVel");
  //Serial.print(SensorI2);
  //Serial.print("\t");
  //Serial.print(SensorI1);
  //Serial.print("\t");
  //Serial.print(SensorD1);
  //Serial.print("\t");
  //Serial.print(SensorD2);
  //Serial.print("\t\t");

} // Fin funcion leemos IR


//***********************************************
//****      FUNCIÓN CALCULAMOS POSICIÓN      ****
//***********************************************
void CalculamosPos() {  
  // Calculamos la posicion
  // Fuera de linea es 999
  // Cuando esta fuera de línea tiene que saber cual era la última posición
  // Giramos +/- en función de la posición
  // Cuando no está en linea tiene que seguir el rumbo de la posición anterior o incrementarla
  if((SensorI2>NEGRO)&(SensorI1>NEGRO)&(SensorD1>NEGRO)&(SensorD2>NEGRO)) {
          Serial.println("Fuera de linea");// no cambiamos la Posicion = 999;
          SalidaPinVel=V_MIN;
          }
  else if((SensorI2<NEGRO)&(SensorI1>NEGRO)&(SensorD1>NEGRO)&(SensorD2>NEGRO)) {
          Posicion = -3;
          SalidaPinDir=central-margen;
          SalidaPinVel=V_MIN;
        }
  else if((SensorI2<NEGRO)&(SensorI1<NEGRO)&(SensorD1>NEGRO)&(SensorD2>NEGRO)) {
          Posicion = -2;
          SalidaPinDir=central-margen/2;
          SalidaPinVel=V_MED;
        }
  else if((SensorI2>NEGRO)&(SensorI1<NEGRO)&(SensorD1>NEGRO)&(SensorD2>NEGRO)) {
          Posicion = -1;
          SalidaPinDir=central-margen/4;
          SalidaPinVel=V_MAX;
        }
  else if((SensorI2>NEGRO)&(SensorI1<NEGRO)&(SensorD1<NEGRO)&(SensorD2>NEGRO)) {
          Posicion =  0;
          SalidaPinDir=central;
          SalidaPinVel=V_MAX;
        }
  else if((SensorI2>NEGRO)&(SensorI1>NEGRO)&(SensorD1<NEGRO)&(SensorD2>NEGRO)) {
          Posicion =  1;
          SalidaPinDir=central+margen/4;
          SalidaPinVel=V_MAX;
        }
  else if((SensorI2>NEGRO)&(SensorI1>NEGRO)&(SensorD1<NEGRO)&(SensorD2<NEGRO)) {
          Posicion =  2;
          SalidaPinDir=central+margen/2;
          SalidaPinVel=V_MED;
        }
  else if((SensorI2>NEGRO)&(SensorI1>NEGRO)&(SensorD1>NEGRO)&(SensorD2<NEGRO)) {
         Posicion =  3;
         SalidaPinDir=central+margen;
         SalidaPinVel=V_MIN;
        }

  // Limitamos SalidaPinDir en el margen
  if(SalidaPinDir<central-margen) SalidaPinDir=central-margen;  
  if(SalidaPinDir>central+margen) SalidaPinDir=central+margen;   
  // Ponemos el valor de salida del servo
  Serial.print("\tDir=");
  Serial.print(SalidaPinDir);
  
  // Ponemos la posición
  Serial.print("\tPos=");
  Serial.print(Posicion);
  Serial.print("\t");
} // Fin funcion calcula la posición


//***********************************************
//****        FUNCIÓN PONEMOS MOTORES        ****
//***********************************************
void PonemosMotores(int VelIzq, int VelDer) {
// Si la velocidad es menor que 10 no hacemos nada  
        //MOTOR D
        //if((VelDer>10)||(VelDer<-10)){ // No tenemos en cuenta valores menores que 10
              if(VelDer>=0) {
                  analogWrite(MDA,VelDer);
                  analogWrite(MDB,0);
              } else {
                  analogWrite(MDA,0);
                  analogWrite(MDB,-VelDer);          
              }
        //}
        
        //MOTOR I
        //if((VelIzq>10)||(VelIzq<-10)){ // No tenemos en cuenta valores menores que 10        
              if(VelIzq>=0) {
                  analogWrite(MIA,VelIzq);
                  analogWrite(MIB,0);
              } else {
                  analogWrite(MIA,0);
                  analogWrite(MIB,-VelIzq);          
              }
  //}
  // Ponemos información motores
  Serial.print("\t VI=");
  Serial.print("\t");
  Serial.print(VelIzq);
  Serial.print("\t VD=");
  Serial.print("\t");
  Serial.print(VelDer);
} // Fin función ponemos motores

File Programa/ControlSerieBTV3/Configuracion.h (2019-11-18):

// Pines Botón de inicio / parada y claxon
#define CLAXON 9  // Pulsador para el claxon, puesto a pullup
#define BOTON  8  // Pulsador de inicio parada, puesto a pullup
                  // La lectura da siempre positivo, salvo que se pulse el botón
#define BUZZER 10  // Reservado para poner el altavoz del claxon
#define CONTROLir 12// Futuro control de los sensores por este pin

// Definición pines motores PWM
#define MDA 3  // Negro
#define MDB 5  // Blanco
#define MIA 11 // Violeta
#define MIB 6  // Negro

// Definición pines controles manuales y servo
// Pines sensores infrarrojos
#define SIRD2 A1
#define SIRD1 A2
#define SIRI1 A3
#define SIRI2 A4

#define BATERIA  A0  // Pin analógico para medición de batería. Divisor con dos resistencias de 10K
#define PinServo  4  // Salida control servo
#define central  85  // Es la configuraion del servo en posición central
#define margen   35  // Apertura lateral desde la posición central. Límite
#define retardo  20  // Posible retardo en los bucles

// Lecturas de línea
//¡EN LA OSHWDEN 2019 TENÍA ESTE VALOR DE NEGRO A 100
// En casa con cinta aislante negra y con papel impreso en tinta este valor
// funionaba muy bien, pero el negro de la pista OSHWDEM es muy brillante y 
// refleja algo más de luz. TSELA no era capaz de distingur el negro y ahí se quedó.
// Con 500 creo que no hace falta ni calibrar. He probado con colores, con grises y bien.
#define NEGRO 500    // Por debajo de 100 es color negro
#define BLANCO 500   // Mas de 500 (999) es blanco

#define V_MAX 250  // Va muy bien con 250 / 150 / 100
#define V_MED 200  // Tambien con 250 / 170 /150
#define V_MIN 150

// Otros parámetros de configuracion
#define NumLecturas 10 // Serán las lecturas para hacer la media
